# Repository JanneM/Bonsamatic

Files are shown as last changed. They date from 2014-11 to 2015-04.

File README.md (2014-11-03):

# Bonsamatic

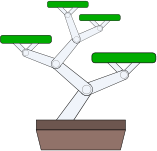
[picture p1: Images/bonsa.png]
Bonsa
 

Bonsamatic is a small-size timer plant watering system, devised to keep my bonsai alive and well during travel. 

## Bonsamatic features:

* A good quality Japanese-made membrane pump for reliable water dosage.

* Water-resistant design that let me leave it out on the balcony without worrying about rain. The box, the meter and 12V power plug are sealed, and the top switch is rated for outdoor use.

* A stylish, easy to read analog time meter and tactile analog controls. You can easily set a time from 6 hours to 10 days at the twist of a dial, and see the time left at a glance.

* Custom-designed(1) Arduino breadboard with all electroncis for control, the UI and motor control on a single board. 

* Quality(2) embedded control software that has been tested literally handfuls of times.

* An LED. Every project needs an LED. 

Bonsai need water on a very regular schedule, but don't like being constantly wet. Bonsamatic 1.0 relies on a timer for watering, rather than a moisture sensor. This works fine for a period of a week or two. If you want a water system that can work indefinitely you need to measure the soil moisture content. A proper moisture sensor and a wifi connection is on the to-do list, but it is quite difficult to make a good, reliable moisture sensor so it will not happen in the near term.

The most interesting part of this project is perhaps not the water system itself, but the time display. The time frame ranges from hours to several days, so a logarithmic scale is all but necessary. However, I use a cheap(3) analog dial, and its voltage response is anything but regular. And as the Atmel AVR pwm has only 8 bit resolution, we need to figure out how to map the display response directly to the scale we want with minimal inaccuracy.

*Software/analogdisplay.py*

This script will figure out the displayed time for each pwm output level given the measured voltage/degree response of the dial and the desired time range. The dial I use has a linear response at 0-20 degrees, and a logarithmic response beyond that so the code reflects this. The script is thus not really a general solution but an example of how to figure this out.

It generates a couple of tables for use in the Arduino sketch, and, if you have "svgwrite" installed, an SVG graphic of the dial scale to print out and use in the dial.The source code is documented and shows how to use the script.

*Bonsamatic/Bonsamatic.ino*

This is the Arduino sketch that runs Bonsamatic. It's a fairly simple event-driven loop that uses the table data generated by analogdisplay above to drive the dial display.

*Doc/bonsa_schem.svg
Doc/bonsa_bom.html
Doc/bonsa.fzz*

This is the schematics for the Bonsamatic hardware, the bill of materials, and the Fritzing design file. Note that these files show generic components, not the exact ones I used, and the analog dial component is badly implemented by myself and won't probably even show up in these files.

If you have any questions or comments, you can contact me at jan.moren@gmail.com

All files are copyright 2014 Jan Moren and licensed under GPL version 3.

_(1) "custom" as in "I made it up as I went along"._

_(2) The word "high" appears nowhere in the vicinity of "quality". This is not an accident._

_(3) I looked for the lowest-cost analog voltage dial at my local electronics store, and yes, you get what you pay for._

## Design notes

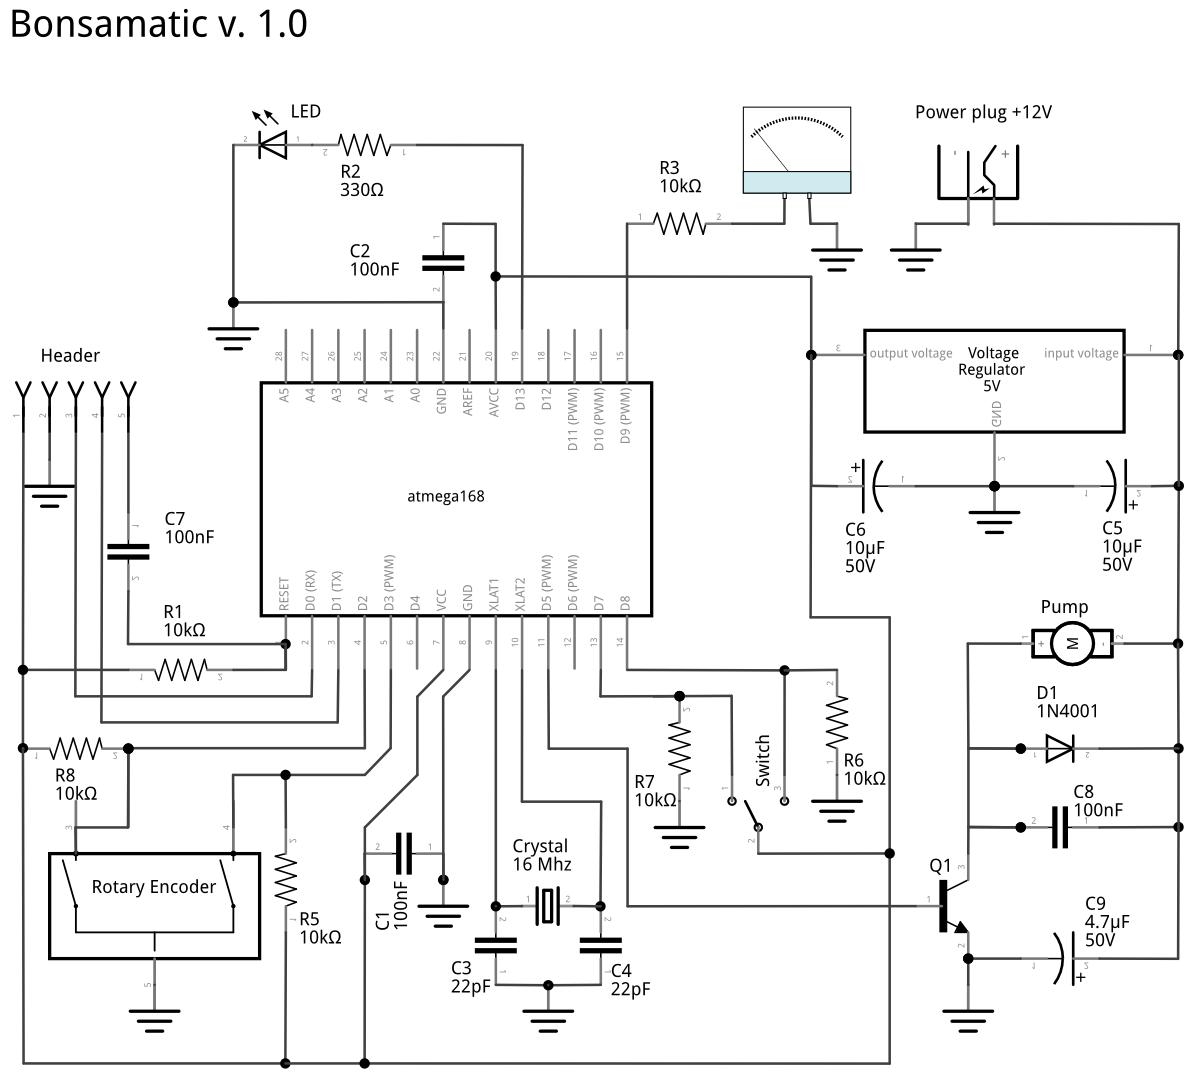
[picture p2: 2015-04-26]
Doc/bonsa_schem.png

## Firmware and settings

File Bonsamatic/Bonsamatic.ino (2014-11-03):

// Bonsamatic sketch with time setting and analog output display
//
// Copyright 2014 Jan Moren
//
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

#define DEBUG false

// We put the lookup table in PROGMEM to save RAM memory space
#include <avr/pgmspace.h>

// cumulative time left in seconds for a given value of output.
// generated as tleft in analogdisplay.py
const prog_uint32_t tleft[] PROGMEM = {
      0,    823,   1659,   2508,   3370,   4246,   5137,   6041,
   6959,   7893,   8841,   9804,  10782,  11776,  12786,  13811,
  14853,  15912,  16987,  18079,  19189,  20316,  21462,  22625,
  23807,  25007,  26227,  27466,  28725,  30003,  31302,  32622,
  33962,  35324,  36708,  38113,  39541,  40991,  42464,  43961,
  45481,  47026,  48595,  50189,  51808,  53453,  55125,  56822,
  58547,  60299,  62457,  65385,  68329,  71290,  74265,  77256,
  80262,  83283,  86319,  89370,  92434,  95513,  98606, 101713,
 104834, 107968, 111116, 114276, 117450, 120637, 123837, 127050,
 130275, 133512, 136762, 140024, 143298, 146584, 149882, 153192,
 156514, 159847, 163191, 166547, 169914, 173292, 176681, 180081,
 183492, 186914, 190346, 193789, 197243, 200707, 204181, 207666,
 211160, 214665, 218180, 221705, 225240, 228785, 232339, 235903,
 239477, 243060, 246653, 250255, 253867, 257488, 261118, 264757,
 268405, 272062, 275729, 279404, 283088, 286781, 290483, 294194,
 297913, 301640, 305377, 309122, 312875, 316637, 320407, 324185,
 327972, 331767, 335570, 339381, 343200, 347027, 350863, 354706,
 358557, 362416, 366283, 370157, 374040, 377930, 381828, 385733,
 389646, 393566, 397494, 401430, 405373, 409323, 413281, 417246,
 421218, 425198, 429184, 433178, 437179, 441188, 445203, 449225,
 453255, 457291, 461335, 465385, 469442, 473506, 477577, 481655,
 485740, 489831, 493929, 498034, 502145, 506263, 510388, 514519,
 518657, 522801, 526952, 531109, 535273, 539443, 543619, 547802,
 551992, 556187, 560389, 564597, 568812, 573032, 577259, 581492,
 585731, 589977, 594228, 598486, 602749, 607019, 611294, 615576,
 619864, 624157, 628457, 632762, 637073, 641390, 645713, 650042,
 654377, 658717, 663064, 667415, 671773, 676136, 680506, 684880,
 689261, 693647, 698038, 702436, 706838, 711247, 715661, 720080,
 724505, 728935, 733371, 737813, 742259, 746711, 751169, 755632,
 760100, 764574, 769053, 773537, 778027, 782522, 787022, 791527,
 796038, 800554, 805075, 809601, 814133, 818669, 823211, 827758,
 832310, 836867, 841429, 845996, 850569, 855146, 859728, 864316};

// The set times data structure. It's small enough that we don't bother
// putting it in progmem.

typedef struct {
  unsigned long t;    // actual time set in seconds
  int idx;            // index to closest step in tleft
} 
set_times_struct;

const int n_times = 16;

set_times_struct set_times[n_times] = {
{     0,   0},	 //   0 hours
{ 21600,  22},	 //   6 hours
{ 43200,  38},	 //  12 hours
{ 64800,  51},	 //  18 hours
{ 86400,  58},	 //  24 hours
{129600,  72},	 //  36 hours
{172800,  85},	 //  48 hours
{216000,  97},	 //  60 hours
{259200, 109},	 //  72 hours
{345600, 133},	 //  96 hours
{432000, 155},	 // 120 hours
{518400, 176},	 // 144 hours
{604800, 196},	 // 168 hours
{691200, 216},	 // 192 hours
{777600, 236},	 // 216 hours
{864000, 255}	 // 240 hours
};

// Analog display
int out_display = 9;	    // port

// light LED 
int led = 13;		    // port
unsigned long led_time;	    // counter for blink rate
int led_state;		    // on or off

// Rotary encoder
int in_A = 3;		    // port
int in_B = 2;		    // port
int last_A = HIGH;	    // hold state to determine direction

// Pump
int pump = 12;		    // port
int pumptime = 30*1000;	    // watering time; determines total water volume
unsigned long water_time;   // clock time at which we started watering
bool watering = false;	    // are we watering or not

// Mode switch
int in_run = 7;		    // port
int in_set = 8;		    // port

// timing data
unsigned long end_time;     // absolute time to start watering
unsigned long next_time;    // absolute time to take the next step down 
int cur_idx = 0;            // current voltage index: 0 <= cur_ind <= 255
int set_idx = 5;	    // set time index 0<= set_idx < n_times
// state
#define NO_STATE 0	    // turned off
#define RUN_STATE 1	    // counting down or watering
#define SET_STATE 2	    // setting the time
char mode = NO_STATE;

//
// functions
//
  
void setup() {

  // Set up all ports
  if (DEBUG) Serial.begin(9600);
  pinMode(in_A, INPUT);
  pinMode(in_B, INPUT);
  pinMode(in_run, INPUT);
  pinMode(in_set, INPUT);
  pinMode(led, OUTPUT);
  pinMode(pump, OUTPUT);

  start_countdown();

  // set the led blink state
  led_time = millis();
  led_state = HIGH;
}

// translate from seconds to milliseconds.
// also useful for debugging.
inline unsigned long s_to_ms(unsigned long sec) {
  return sec*1000;
}

// read a tleft table index from PROGMEM
inline unsigned long read_tleft(int idx) {
  return s_to_ms(pgm_read_dword_near(tleft+idx));  
}

// fix the watering time and set the initial index time
void start_countdown() {

  if (DEBUG) Serial.print("start countdown: ");
  
  unsigned long get_time = millis();
  cur_idx = set_times[set_idx].idx;

  // now + the total waiting time = when we should water.
  end_time = get_time+s_to_ms(set_times[set_idx].t);
  unsigned long nt = read_tleft(cur_idx);

  // when do we next step down the analog counter?
  next_time = end_time-nt;  
  if (next_time > get_time) 
    next_time = get_time;

  if (DEBUG) {
    Serial.print(end_time);
    Serial.print(" - ");  
    Serial.print(nt);
    Serial.print(" = ");
    Serial.print(next_time);
    Serial.print("\n");
  }
  
  // set the display to the current value
  analogWrite(out_display, cur_idx);   
}  

// we start the watering procedure
void start_water() {

  if (DEBUG) Serial.print("start water: ");
  
  // now + pumptime = when to stop the pump
  water_time = millis() + pumptime;
  
  if (DEBUG) Serial.print(water_time);
  if (DEBUG) Serial.print ("\n");
  
  // start pumping
  digitalWrite(pump, HIGH); 
  watering = true;
}  
 
// stop the water and restart the countdown from the beginning
void stop_water() {

  if (DEBUG) Serial.print("stop water\n");

  digitalWrite(pump, LOW);
  watering = false; 
  start_countdown();
} 

// Check if it's time to stop the water yet
void do_water() {

  unsigned long get_time = millis();
  if (get_time > water_time) {
    stop_water();
  }
}

// the main countdown procedure, called in a loop
void do_countdown() {

  // We start watering once the clock time passes the end time 
  // we set at the start_countdown
  unsigned long get_time = millis();
  if (get_time >= end_time) {
    start_water();    
  } 

  // if we surpass the time to step down the counter, we do so, and 
  // figure out the time to step it down the next time in turn.
  else if (get_time >= next_time) {
    cur_idx--;
    unsigned long nt = read_tleft(cur_idx);
    next_time = end_time-nt;
    analogWrite(out_display, cur_idx);   
  }  
}

// when setting the time, keep the time index in the valid range, and set the
// dial to reflect the current choice.
int set_time(int sidx) {

  if (sidx < 0) {
    sidx = 0;
  }
  if (sidx >= n_times) {
    sidx = n_times-1;
  }

  analogWrite(out_display, set_times[sidx].idx);
  return sidx;
}

// Blink the LED while we're in the time set mode
void set_led() {

  unsigned long now_time = millis();

  if ((led_time + 500UL) < now_time) {

    if (led_state == HIGH) {
      led_state = LOW;
    } else {
      led_state = HIGH;
    } 
    led_time = now_time;
  }    
  digitalWrite(led, led_state);
}

// check the state of the rotary dial and set the desired time based on that.
void do_set_time() {
  int A_state = digitalRead(in_A);

  if ((last_A == HIGH) && (A_state == LOW)) {
    int B_state = digitalRead(in_B);

    if (B_state == HIGH) {            // clockwise
      set_idx = set_time(set_idx+1);
    } 
    else {                            // counterclockwise
      set_idx = set_time(set_idx-1);
    }
  }
  last_A = A_state;
  set_led();  
}  

 
void loop() {

  // we're setting the time
  if (mode==SET_STATE) {
    do_set_time();
  }

  // we're counting down or watering
  if (mode==RUN_STATE) {
    if (watering == false) {
      do_countdown();		
    } else {
      do_water();	    
    }
  }
  
  delay(1);

  // we read the state of the set switch and determine if
  // we're setting the time, running, or are turned off.
  int set_switch = digitalRead(in_set);
  int run_switch = digitalRead(in_run);

// Set the time
  if (set_switch == HIGH) {
    if (mode != SET_STATE) {
      mode = SET_STATE;
      led_time = millis();
      led_state = HIGH;
      stop_water();
    }
  }

// Run the countdown
  if (run_switch == HIGH) {
    if (mode != RUN_STATE) {
      mode = RUN_STATE;
      start_countdown();
      digitalWrite(led,HIGH);
    }
  }

// Turn off.
  if ((run_switch == LOW) && (set_switch == LOW)) {
    if (mode != NO_STATE) {
      mode = NO_STATE;
      digitalWrite(led, LOW);
      stop_water();
    }
  }
}

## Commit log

2014-05-26 initial working code. No pump driver yet.
2014-06-02 generated a meter display. Not quite right, but close enough.
    [Bonsamatic.fzz]
2014-06-08 added pump activation, led blink
2014-06-08 pump timer fixes
2014-06-10 set pump time to 20 seconds. 30 is too long
    [Bonsamatic.ino]
2014-08-03 fixed a bug, added some debugging stuff
    [Bonsamatic.ino]
2014-11-02 cleanups, reorganize directories
    [Bonsamatic.fzz, bonsa.fzz]
2014-11-02 tweak pump time
2015-04-26 add png version of the schematic. Seems Github doesn't render the svg file correctly

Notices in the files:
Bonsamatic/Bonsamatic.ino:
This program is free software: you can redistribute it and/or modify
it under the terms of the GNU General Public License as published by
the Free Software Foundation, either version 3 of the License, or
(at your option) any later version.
